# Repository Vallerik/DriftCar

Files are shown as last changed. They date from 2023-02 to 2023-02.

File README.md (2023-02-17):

DriftCar
====
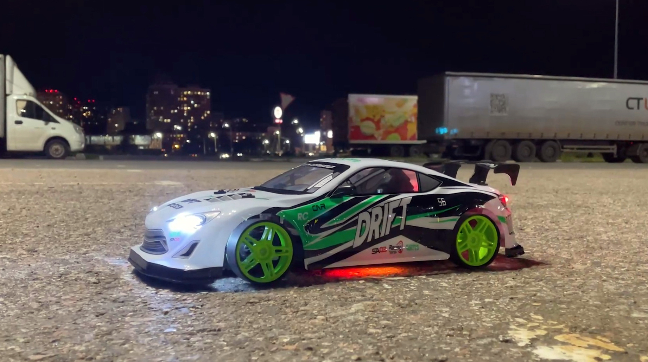
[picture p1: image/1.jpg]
DriftCar

In this project, I showed the completion of a drift car with a complete alteration of electronics and the addition of lighting and music.
What a drift machine is initially capable of:
- The charge of the native battery is enough for 10 minutes, after 7 minutes the car just drives without drifting;
- Discrete control;
- Police lighting;
- Drift around;
- Drift eight.

[Video review of drift cars without modifications.](https://youtu.be/6MPHbPOtivM)

What do I want to do?
- Make front and rear lights;
- Introduce completely your own homemade electronics with proportional steering and gas control;
- Write a program for the typewriter and remote control;
- Put 3S battery;
- Add music to the machine with the ability to switch it from the remote control;
- Make the backlight on the addressable LEDs with the ability to switch it from the remote control;
- Servo steering wheel control.

[Video about drift cars with all the modifications.](https://youtu.be/wygo5vjzIAw)

Required components
====
For electronics, you will need the following components:

For the machine:
- Arduino Nano - 1 piece;
- Servo MG90D - 1 piece;
- HC-12 - 1 piece;
- Board with addressable LEDs - 2 pieces;
- Wires;
- Player DY-SV5W - 1 piece;
- microSD memory card - 1 piece;
- Speaker AIYIMA 5W 4 om - 1 piece;
- Racks for a column - 2 pieces;
- Hardware for the column and brass racks;
- LEDs white 5 mm - 2 pieces;
- LEDs white 3 mm - 4 pieces;
- LEDs red 5mm - 2 pieces;
- Resistors 100 ohm - 6 pcs, 150 ohm - 2 pcs, 200 ohm - 1 pc, 10 kOhm - 1 pc;
- Connectors XH 2.54 3P female - 4 pcs;
- Connectors XH 2.54 3P male - 4 pcs;
- Connector JST SM 2.54 2P female - 1 piece;
- Printed circuit boards.

For remote control:
- Arduino Nano - 1 piece;
- HC-12 - 1 piece;
- Charging board TP4056 with step-up DC-DC converter - 1 piece;
- CJMCU-103 - 2 pieces;
- Two-color LED with a common cathode - 1 pc;
- Resistors 150 ohm - 1 piece, 160 ohm - 1 piece;
- DIP Buttons - 2 pieces;
- Wires;
- Connector JST SM 2.54 2P female - 1 piece;
- Breadboard - 1 piece;
- LiPo 400mA - 1 piece.

For battery:
- Li-ion NCR 18650 with wires - 3 pieces;
- BMS 3S with balancing - 1 piece;
- Connector JST SM 2.54 2P male - 1 piece;
- Wires.

Revision history
====
I started reworking the machine by disassembling and studying its device. I took off all the native electronics with the steering mechanism and began to think about how and where to place all the components.
In this project, I have identified two difficult places for rework:
1. Steering.
I have a rough idea of how the steering should work on a servo, but how to place it and will the small servo have enough power? For me, these were the main questions and fears.
2. Alteration of the remote control.
Since the native equipment of the drift car has discrete control, it will be difficult to convert it to proportional control, according to my feelings, because you need to somehow build variable resistors into the remote control,
and what if it doesn't work? Well, as they say, the eyes are afraid, but the hands do!

It is very important in projects to find difficult places or things that cause the most problems, these things need to be done first and after solving all the difficult tasks, do everything else.
It would be very stupid to abandon the project at an almost finished stage, when all the simplest things have already been done, but you cannot complete the project because of 2 difficult tasks that you decided to postpone.
As a result, you get an abandoned project that needs to be redone or finalized.

After studying the device, I had several options for the location of the components, first of all, I tested the servo and decided on its power.
I thought over the steering mechanism, the location of the servo drive and the device of the control panel. In order to finally decide on the device of the machine and the remote control, then it is necessary to prepare the electronics.
I wrote a program in the Arduino IDE, assembled and debugged the prototype, after that I made a circuit diagram of the electronics of the machine and the remote control.

The device of the new steering mechanism
====
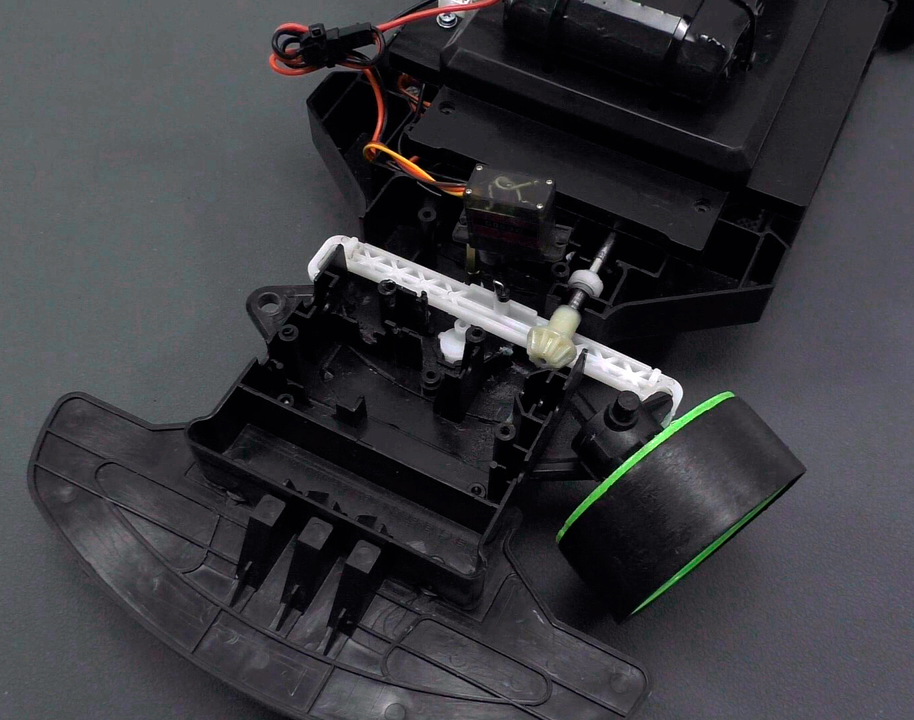
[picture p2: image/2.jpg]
The device of the new steering mechanism

The ideal place to fix the servo coincides with the plastic stand in the case. The second ear of the servo is already screwed to the brass stand in place. 
In the central position of the servo, a rocker with a drilled groove is screwed. A curved pin glued into the steering rack is inserted into this groove. 
The pin is made from the original spring of the steering gear, teeth for the gear were bitten off from the rack itself.
And the only important point, you need to install the rocker in the central position of the servo (90°) and the servo itself is screwed through a spacer printed on a 3D printer. 
The servo drive, turning the rocker, moves the pin along the groove, thereby setting the steering rack in motion. The mechanism works perfectly, 
there is enough servo power, there is no jamming, and I was even surprised how well the arrangement of the components coincided.

Location of electronics
====
In the compartment for the old battery, I screwed the board from the player onto the plastic racks, and fastened the speed controller to the plastic ties.

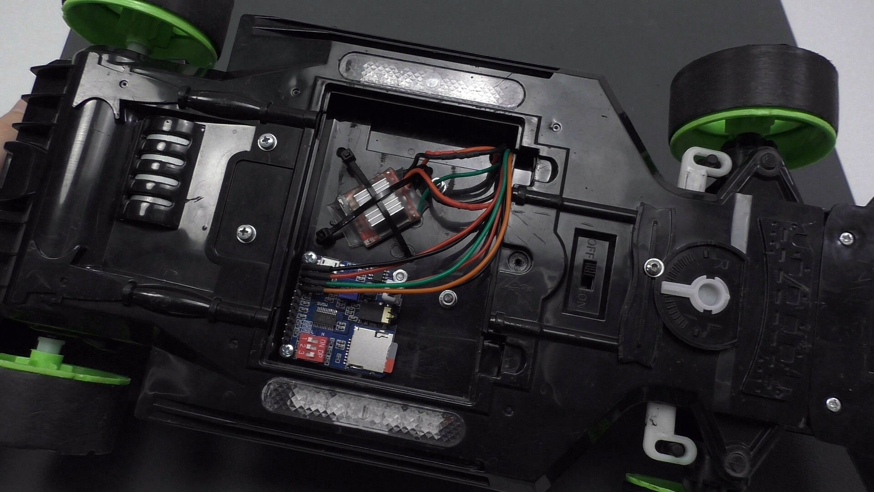
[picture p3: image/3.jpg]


By the way, this regulator needs to be improved to prevent its heating when powered by a 3S battery. The fact is that this speed controller, according to the seller, only supports a 2S battery.
When a 3S battery is connected, the regulator also works, but the diode and transistor start to heat up, I dropped these components, the printed circuit board stopped heating and the regulator works properly.
All components on the PCB support voltages above 12 volts, so everything is fine.

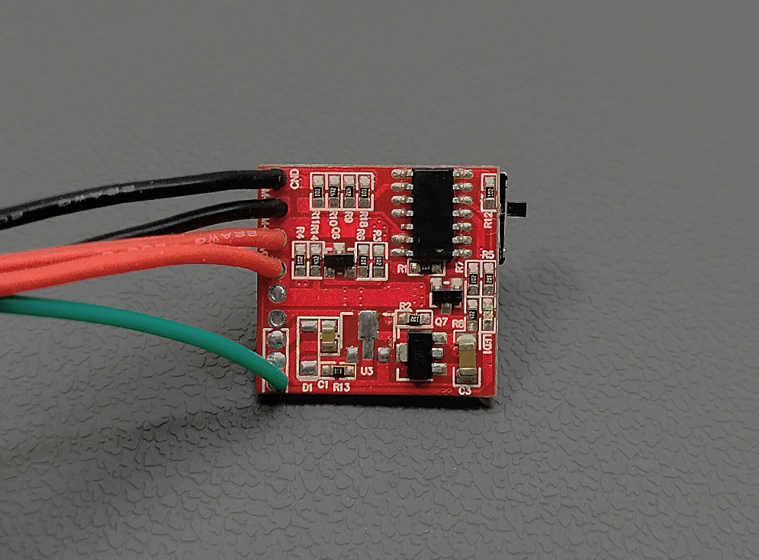
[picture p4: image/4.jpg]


Under the central cover in the middle, there is a board with an Arduino Nano, after which a power board is installed and panels with addressable LEDs are glued on the sides.
The native switch in the front is used to turn off the power, some holes were also made in the case for wires, well, the whole bunch of wires, if possible, was fastened with plastic ties.

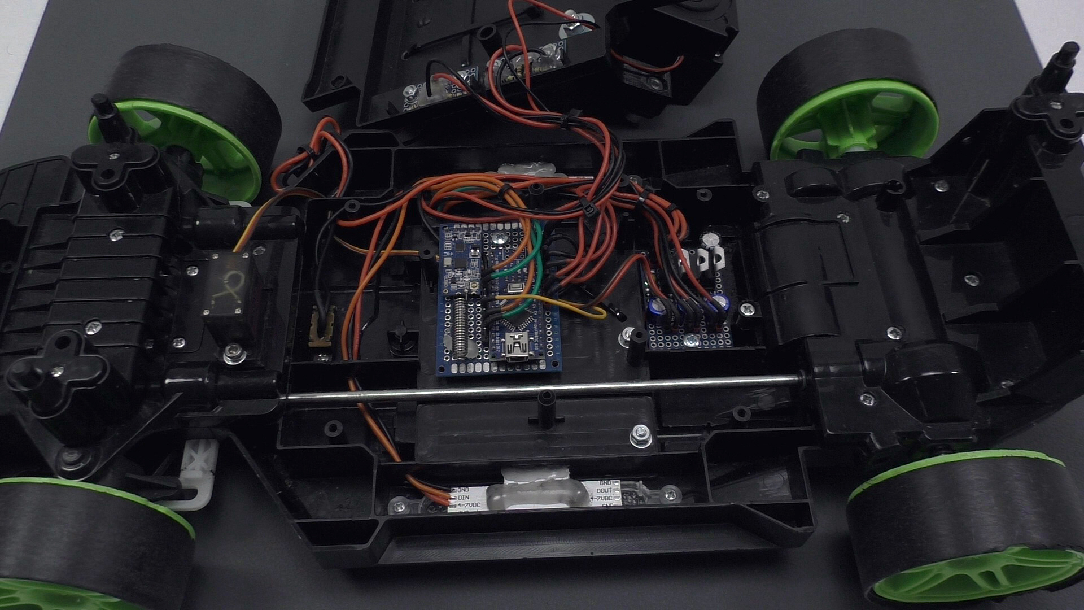
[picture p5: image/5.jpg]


All electronics are connected according to this scheme:
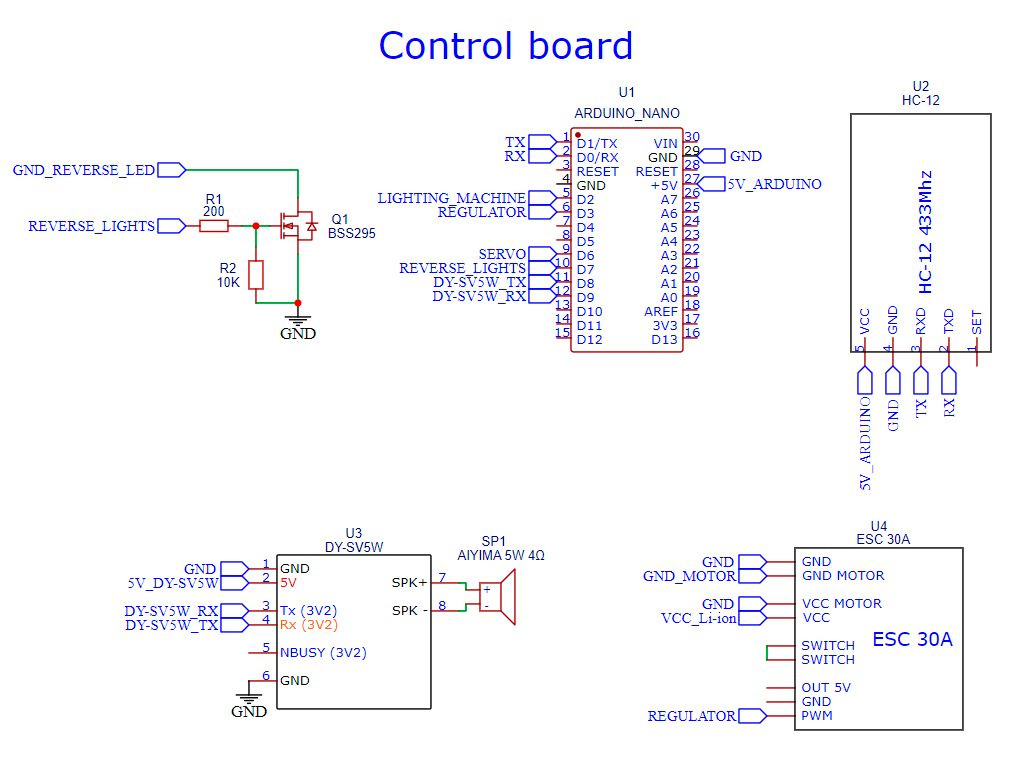
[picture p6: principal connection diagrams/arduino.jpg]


Printed circuit boards
====

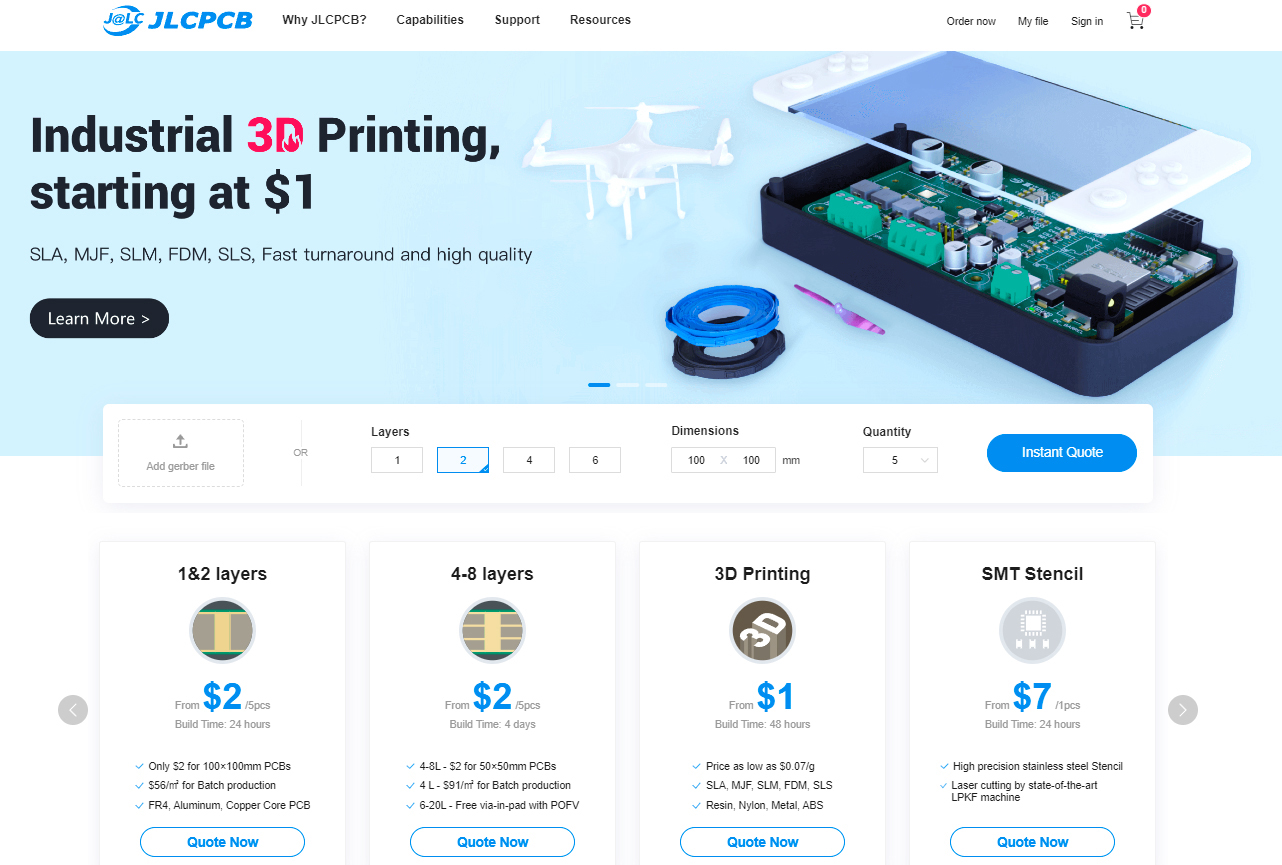
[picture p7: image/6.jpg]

In order not to suffer like me with the manufacture of boards on a breadboard, I recommend ordering the manufacture of printed circuit boards from [JLC PCB](https://jlcpcb.com/RHS). 
This is the largest enterprise for the production of printed circuit boards of industrial quality, of any complexity, of any size.
For just $2 plus shipping, [JLC PCB](https://jlcpcb.com/RHS) will make you five 2-layer 100x100mm PCBs, or five 4-layer 50x50mm PCBs! [JLC PCB](https://jlcpcb.com/RHS) can not only manufacture boards, 
but also assemble them on their surface mount equipment. To place an order, you need to upload an archive with gerber files to the site, in the order itself you can configure the necessary parameters, 
such as the color of the mask, the thickness of the textolite, copper and order the assembly of boards, also [JLC PCB](https://jlcpcb.com/RHS) is engaged in 3D printing, 
making stencils for SMT mounting and all this makes in the shortest possible time and with the best quality, so I recommend them.
I made all the listed printed circuit boards from breadboards, soldering the tracks with solder. 
This method of manufacturing printed circuit boards is not always suitable and it is quite difficult to think through the passage of all the tracks, 
and the soldering process itself is complicated if you want to do it neatly and beautifully. Therefore, I recommend ordering printed circuit boards in production, do not suffer, 
do not repeat my mistakes :)

[https://jlcpcb.com/](https://jlcpcb.com/RHS)

GitHub link to download PCB gerber file: 
https://github.com/Vallerik/DriftCar/tree/main/gerber

Battery assembly
====
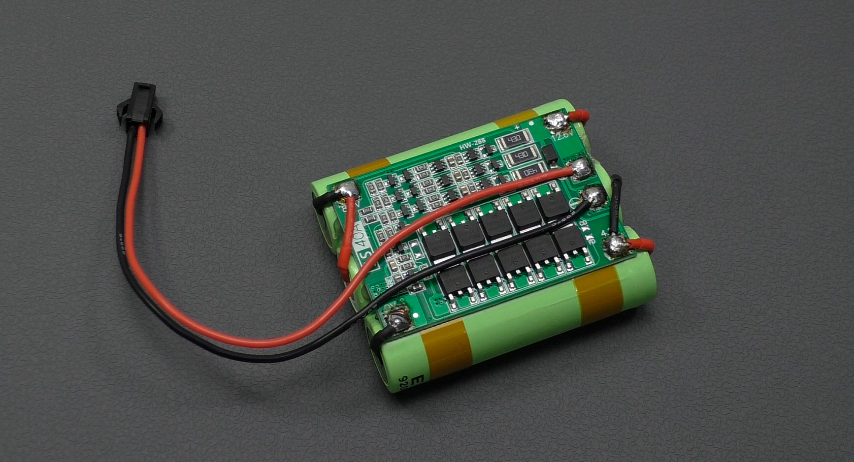
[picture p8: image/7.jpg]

There is nothing complicated in assembling the battery, I think everything is clear just from the photo.
The wires of each can of 18650 are soldered to the corresponding BMS pin of the board, as in this photo.
To connect the battery, a wire with a JST SM 2.54 2P male connector is soldered to the BMS.

Headlights
====
Holes are drilled on the body in the center of all the painted headlights and LEDs are glued with hot glue. 
### Beforehand, it is necessary to solder the wires to the LEDs according to the scheme:
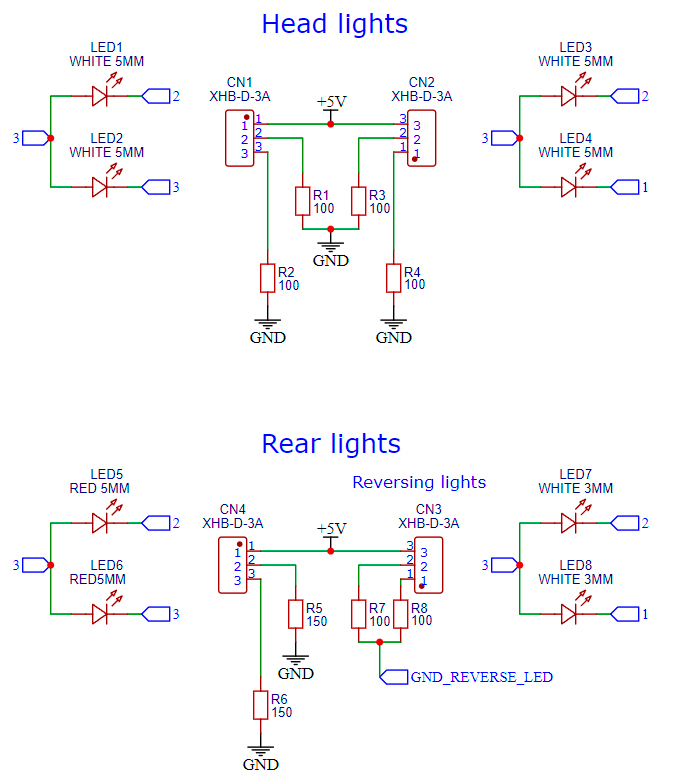
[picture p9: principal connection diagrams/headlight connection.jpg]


The headlights are made from 3 and 5mm white LEDs. Reversing lights made of white 3mm LEDs. The oversized red headlights are made from matte red 5mm LEDs.
The wires from the headlights will be connected to the XH 2.54 3P connectors (Each wire is connected according to its color mark), 
printed circuit boards with these connectors are screwed to the side of the central cover of the machine.

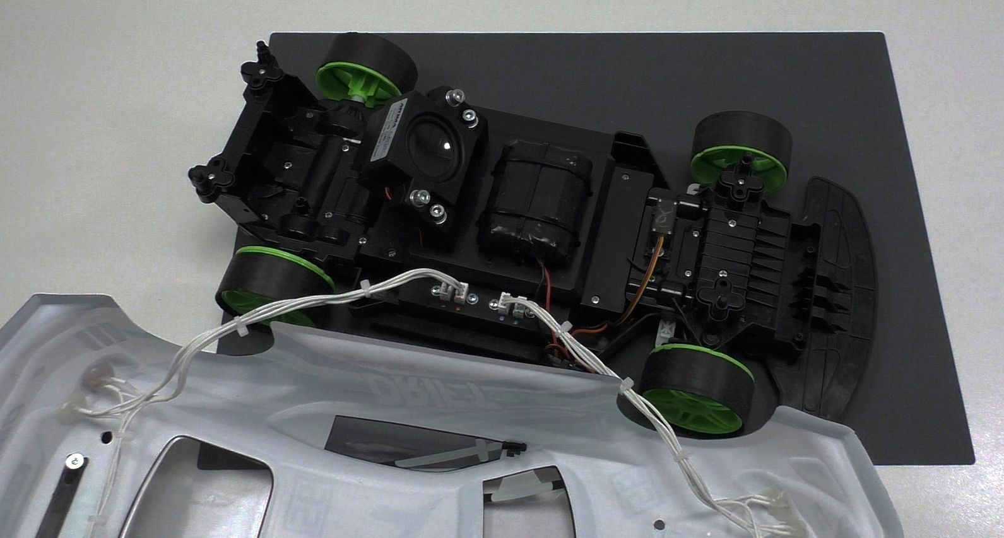
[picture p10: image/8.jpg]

Racks with a speaker are screwed to the same cover and the battery is attached to plastic ties.

Remote control modification
====
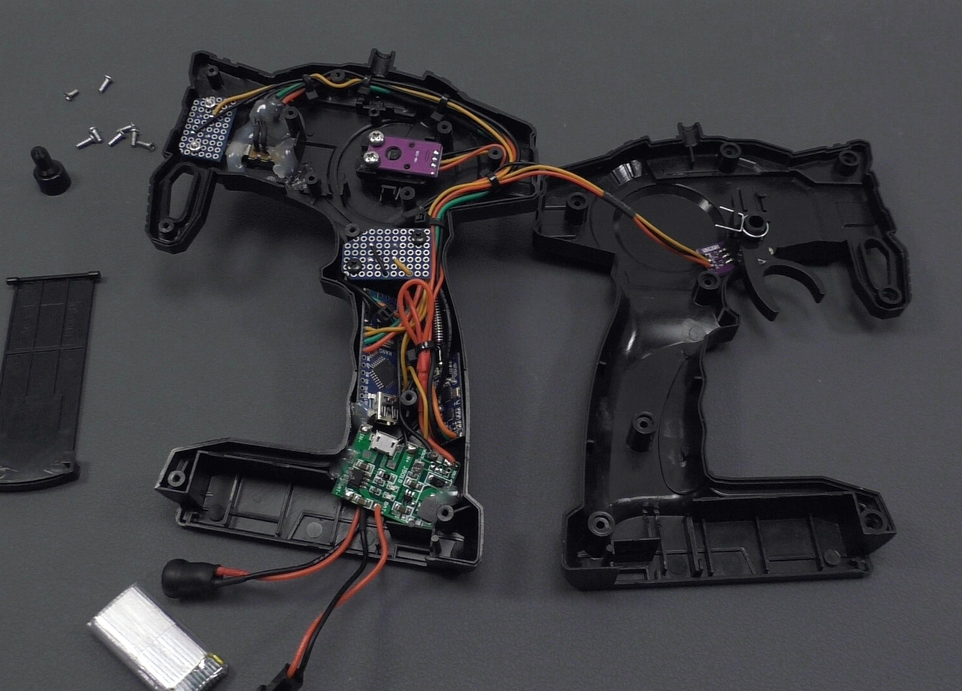
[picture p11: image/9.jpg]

To remake the control panel, the first thing I thought about was how to install the CJMCU-103 modules. To do this, I printed on a 3D printer a special mount and pins for turning the CJMCU-103, 
these pins are glued into the trigger and steering shaft. The first CJMCU-103 steering wheel module is screwed to the mount, and the second CJMCU-103 module is screwed to the control box cover.
Also, for the remote control, two printed circuit boards were cut out for the buttons, a two-color LED was glued in, a switch and a resistor for setting the charging current was changed on the green charging module, 
for a li-po battery with a capacity of 400 mA, I set the charging current to 300 mA. Charging takes place with a USB cable that plugs into a 5.5x2.1 mm jack.
There is nothing else special in the remote control, and well, I also changed my native antenna to a small one printed on a 3D printer. In general, the remote turned out great!
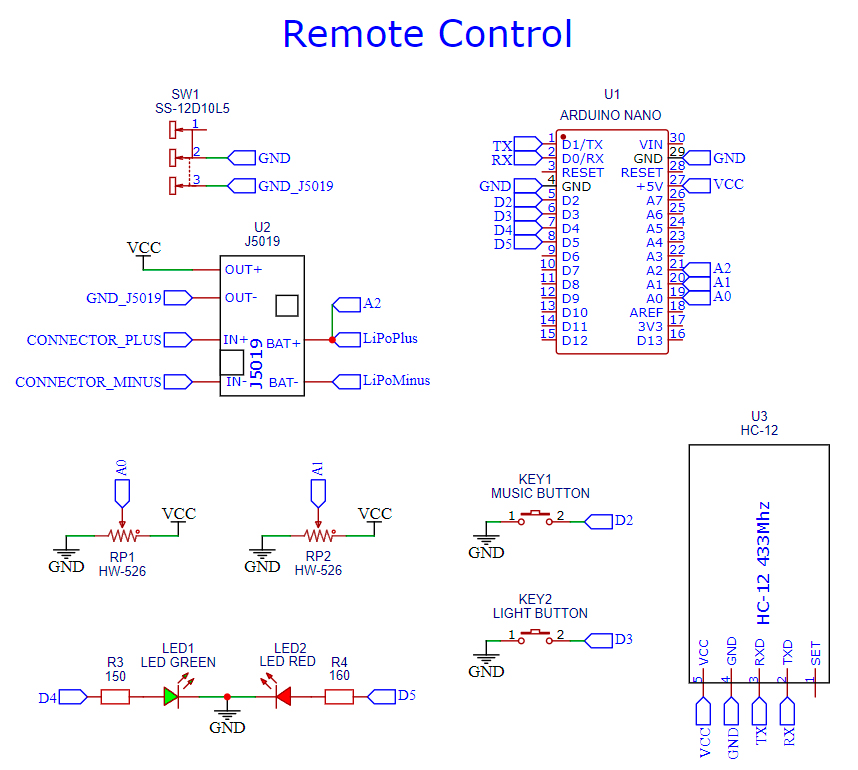
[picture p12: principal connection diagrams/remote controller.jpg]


Project results
====
Now let me summarize, has the car started to drift better? The result, of course, was not the same as I expected, but the car became more cheerful to drive from a 3S battery, due to the proportional control, 
the car became better controlled and, of course, it is better to look with headlights and RGB backlight. A loud speaker makes the bass vibrate and play the whole body, 
these are indescribable sensations of the joy of a working project. My main goal is accomplished, to make a musical drift car with my homemade electronics. From the remote control, 
I can turn on, switch music and backlight, the backlight still has 7 modes of operation, well, in general, I'm exhausted, but satisfied. I will not say that I am an expert in this matter, 
I just set a goal for myself and achieved it. And in this project, I shared my experience and, as a result, I want to warn you that developing your own electronics and modifying such toys is not as easy as it seems. 
If you want to repeat the project after me or do something similar, I would advise you to install ready-made electronics, a receiver, a speed controller, a purchased battery with equipment, 
it will come out easier, cheaper and faster.

Links to other important sources
------------
* [Thingiverse](https://www.thingiverse.com/yourobotics/designs) 3D Model for time-lapse photography.
* [VK group](https://vk.com/yourobotics) My group on the social network "Vkontakte".
* [YouRobotics](https://www.youtube.com/channel/UCt6Rz9BVB6opYcUrAq6mwWA) My YouTube channel.
------------
Made by: Valery Zalit

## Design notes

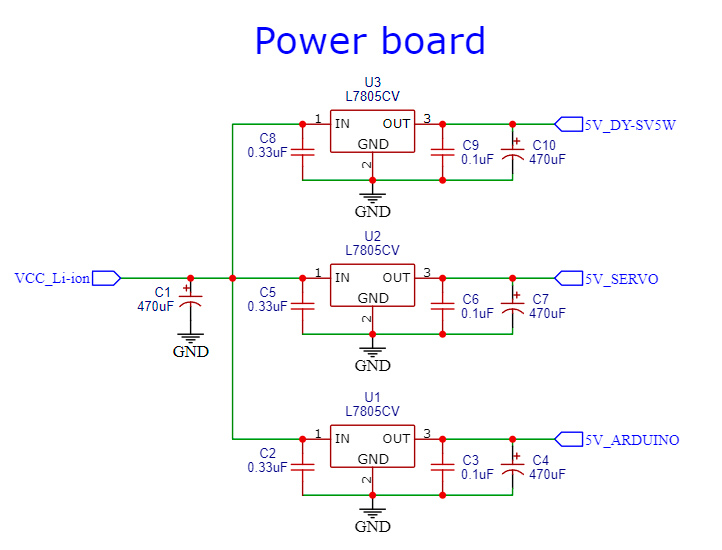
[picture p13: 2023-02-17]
principal connection diagrams/power board.jpg

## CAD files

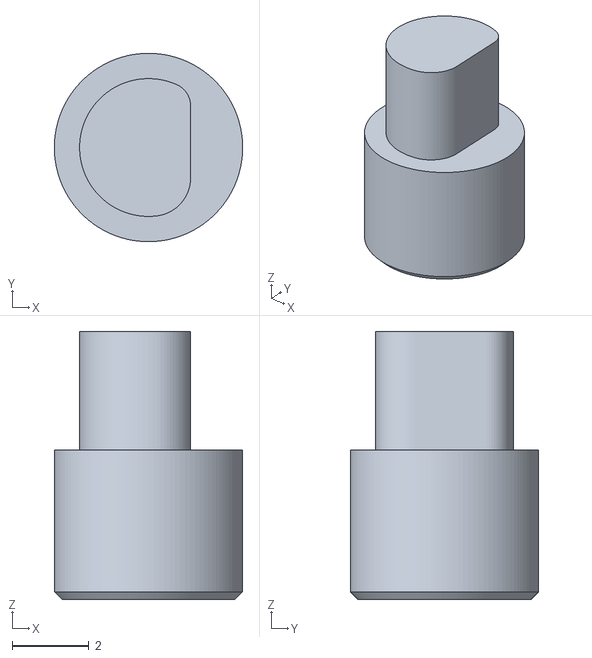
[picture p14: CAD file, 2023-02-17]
3d models/Rudder pin.stl
4.92 x 4.92 x 7.00

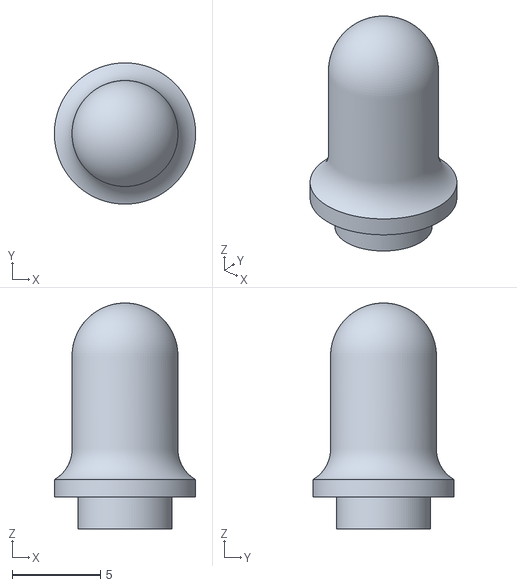
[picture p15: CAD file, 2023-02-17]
3d models/Remote control antenna.stl
8.00 x 8.00 x 12.8

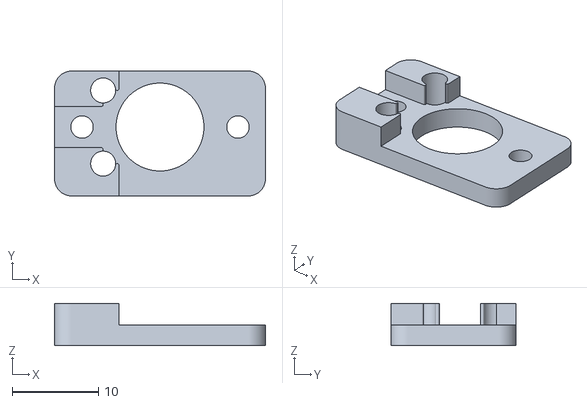
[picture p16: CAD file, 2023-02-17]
3d models/Plate for CJMCU-103.stl
24.5 x 14.5 x 4.90

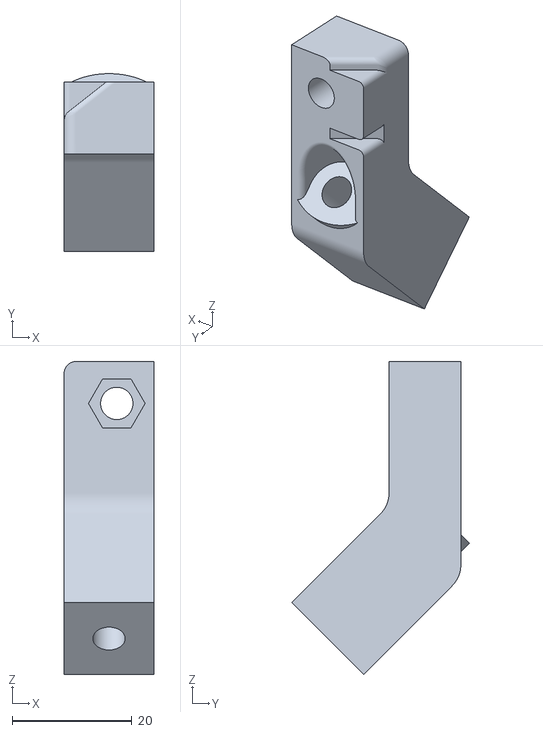
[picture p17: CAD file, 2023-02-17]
3d models/Speaker stand.stl
15.0 x 29.7 x 52.3

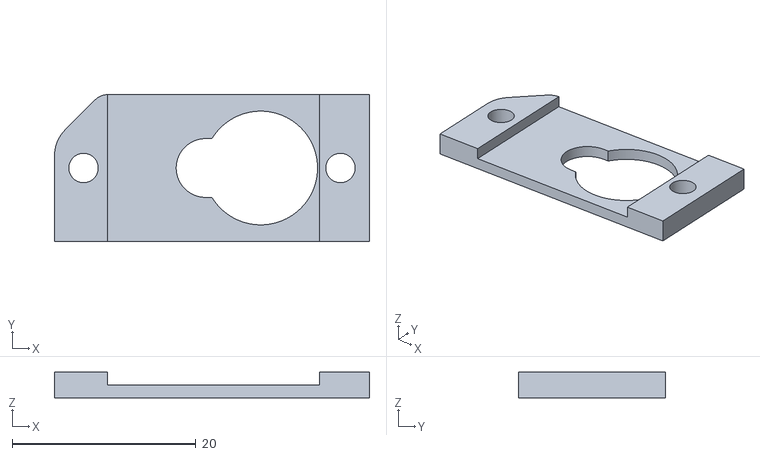
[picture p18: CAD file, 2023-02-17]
3d models/Servo spacer.stl
34.3 x 16.0 x 2.80

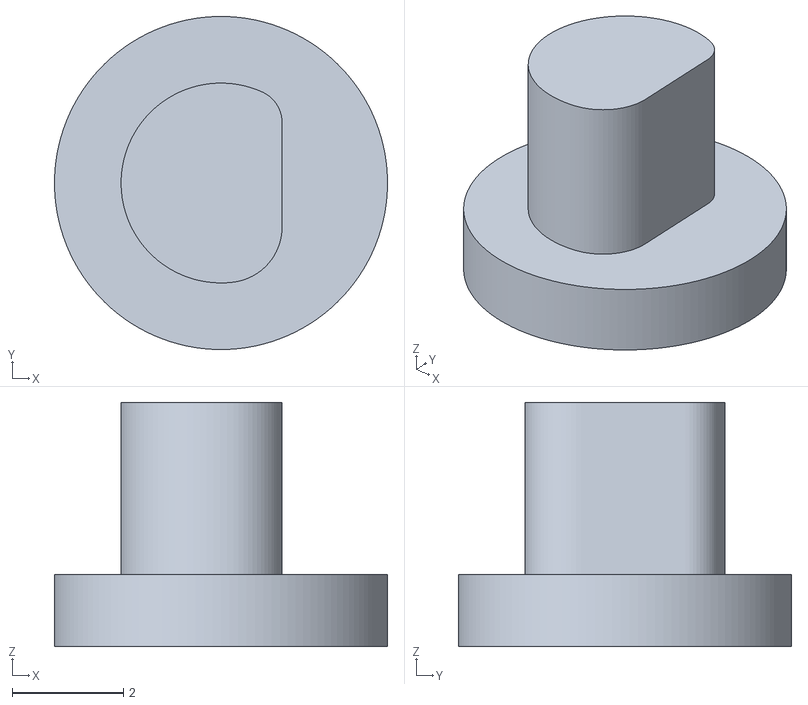
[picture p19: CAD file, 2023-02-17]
3d models/Throttle pin.stl
6.00 x 6.00 x 4.40

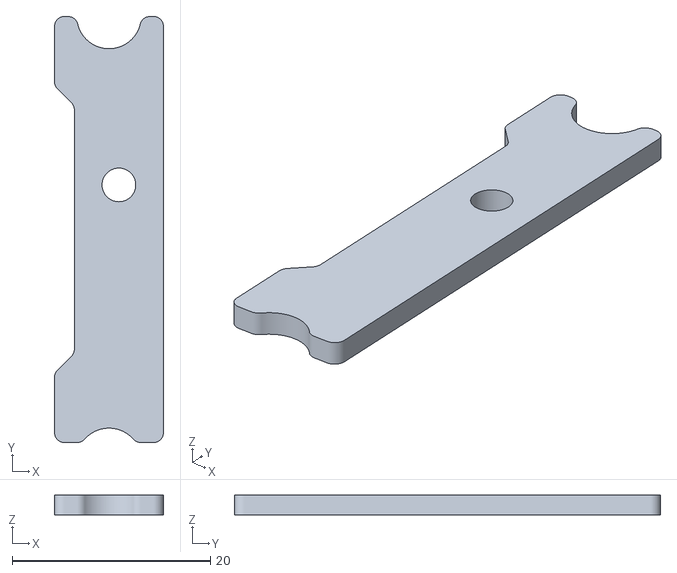
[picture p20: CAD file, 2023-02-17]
3d models/Spacer for servo stand.stl
11.0 x 43.0 x 2.00

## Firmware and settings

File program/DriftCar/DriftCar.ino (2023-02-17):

//Settings
#define MUSIC_OFF_ON_COMMAND 1
#define MUSIC_NEXT_COMMAND 2
#define ON_OFF_BACKLIGHT 3
#define NEXT_ILLUMINATION 4
#define NUMBER_OF_BACKLIGHT_MODES 7 //Number of backlight modes
#define CORNER_CORRECTION -11 //(-право)
#define CENTER_ANGLE 90 CORNER_CORRECTION //Center wheel position
#define MAX_ANGLE 124 //Maximum steering angle
#define MIN_ANGLE 44 //Minimum steering angle

//Libraries
#include <avr/wdt.h>
#include <Arduino.h>
#include "DYPlayerArduino.h"
#include <SoftwareSerial.h>
#include <Servo.h>

#include <LiquidCrystal_I2C.h>

SoftwareSerial mySerial(9, 8); // RX, TX
DY::Player player(&mySerial);
Servo servo;
Servo motor;

#define LEDPIN 2
#define NUMLEDS 8     //Number of LEDs
#include <microLED.h>
#include <FastLEDsupport.h>
microLED<NUMLEDS, LEDPIN, MLED_NO_CLOCK, LED_WS2818, ORDER_GRB, CLI_AVER> strip;

extern CRGBPalette16 myRedWhiteBluePalette;
extern const TProgmemPalette16 myRedWhiteBluePalette_p PROGMEM;

//Pins
#define M_REGULATOR 3
#define RUDDER_SERVO 6
#define REVERSE_LEDS 7


boolean playerStatus = 0;
boolean triggerFlag = 0;
boolean musicStatus = 0;
boolean backlightStatus = 0;
boolean noData = 0;
boolean emergencyStop = 0;

int backlightMode = 0;

unsigned long ledTimer = 0;
unsigned long noDataTimer = 0;

struct Str {
  uint8_t direction;
  int16_t speed;
  uint8_t angle;
  uint8_t command;
};

Str buf;

void setup() {
  Serial.begin(9600);
  mySerial.begin(9600);
  servo.attach(RUDDER_SERVO);
  motor.attach(M_REGULATOR);

  pinMode(REVERSE_LEDS, OUTPUT);

  player.begin();
  player.setVolume(95); //Set the volume to 95%
  player.setCycleMode(DY::PlayMode::Random);
  player.stop();

  strip.setBrightness(64);
  buf.angle = CENTER_ANGLE;

  wdt_enable(WDTO_1S);
}

void ReceiveData() {
  Serial.readBytes((byte*)&buf, sizeof(buf));
}

void PlayerControl(int command) {
  servo.detach();
  motor.detach();

  if (command == 0) {
    musicStatus = 0;  //Turn off the music
    player.stop();
  }

  if (command == 1) {
    musicStatus = 1;  //Turn on the music
    player.play();
  }

  if (command == 2 && musicStatus == 1) {
    player.next();  //Next music
  }

  motor.attach(M_REGULATOR);
  servo.attach(RUDDER_SERVO);
}

void loop() {
  ControlCar();

  if (Serial.available() > 0) {
    ReceiveData();
    noData = 0;
    emergencyStop = 0;
  } else {
    if (noData == 0) {
      noDataTimer = millis();
      noData = 1;
    }
    if (noData == 1 && emergencyStop == 0 && (millis() - noDataTimer) > 500) {
      buf.direction = 0;
      buf.speed = 1500;
      player.stop();
      offLeds(); //Turn off backlight
      backlightMode = 0;
      emergencyStop = 1;
    }
  }

  carBacklight();
  wdt_reset();
}

void ControlCar() {
  if (buf.direction == 0) {
    motor.writeMicroseconds(1500);
    digitalWrite(REVERSE_LEDS, LOW);
  }

  if (buf.direction == 1) {
    motor.writeMicroseconds(buf.speed);
    digitalWrite(REVERSE_LEDS, LOW);
  }

  if (buf.direction == 2) {
    motor.writeMicroseconds(buf.speed);
    digitalWrite(REVERSE_LEDS, HIGH);
  }

  if (buf.angle >= MAX_ANGLE) {
    buf.angle = MAX_ANGLE;
  }

  if (buf.angle <= MIN_ANGLE) {
    buf.angle = MIN_ANGLE;
  }

  servo.write(buf.angle); //Turning the servo

  if (buf.command == MUSIC_OFF_ON_COMMAND && triggerFlag == 0) { //Turning music on and off
    triggerFlag = 1;
    playerStatus = 1 - playerStatus;
    PlayerControl(playerStatus);
  }

  if (buf.command == MUSIC_NEXT_COMMAND && triggerFlag == 0) { //Switching music
    triggerFlag = 1;
    PlayerControl(2);
  }

  if (buf.command == 3 && triggerFlag == 0) { //Turning the backlight on and off
    triggerFlag = 1;
    backlightStatus = backlightStatus - 1;
    backlightMode = 1;

    ledTimer = millis();

    if (backlightStatus == 0) {
      offLeds(); //Turn off the backlight
      backlightMode = 0;
    }
  }

  if (buf.command == NEXT_ILLUMINATION && triggerFlag == 0 && backlightStatus == 1) { //Switching backlight mode
    triggerFlag = 1;
    backlightMode++;
    if (backlightMode > NUMBER_OF_BACKLIGHT_MODES) {
      backlightMode = 1;
    }

  }

  if (buf.command == 0 && triggerFlag == 1) {
    triggerFlag = 0;
  }

}

void offLeds() {
  strip.leds[0] = mBlack;
  strip.leds[1] = mBlack;
  strip.leds[2] = mBlack;
  strip.leds[3] = mBlack;
  strip.leds[4] = mBlack;
  strip.leds[5] = mBlack;
  strip.leds[6] = mBlack;
  strip.leds[7] = mBlack;
  strip.show();
}

void carBacklight() {
  if ( ((millis() - ledTimer) > 40) && backlightStatus == 1 ) {
    motor.detach();
    static byte count = 0;
    static int count2 = 0;
    count = count + 4;
    count2 += 10;
    strip.begin();
    for (int i = 0; i < NUMLEDS; i++) {
      switch (backlightMode) {
        case 1: //Green
          strip.leds[0] = mGreen;
          strip.leds[1] = mGreen;
          strip.leds[2] = mGreen;
          strip.leds[3] = mGreen;
          strip.leds[4] = mGreen;
          strip.leds[5] = mGreen;
          strip.leds[6] = mGreen;
          strip.leds[7] = mGreen;
          strip.show();
          break;

        case 2: //Blue
          strip.leds[0] = mBlue;
          strip.leds[1] = mBlue;
          strip.leds[2] = mBlue;
          strip.leds[3] = mBlue;
          strip.leds[4] = mBlue;
          strip.leds[5] = mBlue;
          strip.leds[6] = mBlue;
          strip.leds[7] = mBlue;
          strip.show();
          break;

        case 3: //Red
          strip.leds[0] = mRed;
          strip.leds[1] = mRed;
          strip.leds[2] = mRed;
          strip.leds[3] = mRed;
          strip.leds[4] = mRed;
          strip.leds[5] = mRed;
          strip.leds[6] = mRed;
          strip.leds[7] = mRed;
          strip.show();
          break;

        case 4:
          strip.send(CRGBtoData(ColorFromPalette(RainbowColors_p, count + i * 3, 255, LINEARBLEND)));
          break;

        case 5:
          strip.send(CRGBtoData(ColorFromPalette(RainbowStripeColors_p, count + i * 3, 255, NOBLEND)));
          break;

        case 6:
          strip.send(CRGBtoData(ColorFromPalette(RainbowColors_p, count + i * 3, 255, LINEARBLEND)));
          break;

        case 7:
          strip.send(CRGBtoData(ColorFromPalette(myRedWhiteBluePalette_p, count + i * 3, 255, NOBLEND)));
          break;

      }
    }
    strip.end();
    motor.attach(M_REGULATOR);
    ledTimer = millis();
  }
}


const TProgmemPalette16 myRedWhiteBluePalette_p PROGMEM =
{
  CRGB::Red,
  CRGB::Gray,
  CRGB::Blue,
  CRGB::Black,

  CRGB::Red,
  CRGB::Gray,
  CRGB::Blue,
  CRGB::Black,

  CRGB::Red,
  CRGB::Red,
  CRGB::Gray,
  CRGB::Gray,
  CRGB::Blue,
  CRGB::Blue,
  CRGB::Black,
  CRGB::Black
};

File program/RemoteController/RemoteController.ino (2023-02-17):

/*
   Remote control program for drift cars
*/

#include <avr/wdt.h>

//Settings
#define MUSIC_OFF_ON_COMMAND 1
#define MUSIC_NEXT_COMMAND 2
#define ON_OFF_BACKLIGHT 3
#define NEXT_ILLUMINATION 4

//Steering wheel
#define CORNER_CORRECTION -11 //Correction of the central position of the wheels (- right, + left)
#define MIN_ANGLE 44 //Minimum steering angle
#define CENTER_ANGLE 90 CORNER_CORRECTION // Servo wheel center position + correction
#define MAX_ANGLE 124 //Max steering angle

#define WHEEL_MINIMUM_RESISTOR_VALUE 377 //Minimum variable resistor value
#define WHEEL_AVERAGE_RESISTOR_VALUE 509 //Average value of the variable resistor
#define WHEEL_MAXIMUM_RESISTOR_VALUE 623 //Maximum value of the variable resistor
#define WHEEL_DEADBAND 5 //Deadband


//Throttle lever
#define SPEED_AVERAGE_RESISTOR_VALUE 543 //Middle speed position
#define SPEED_MAXIMUM_RESISTOR_VALUE 632 // Maximum throttle position
#define SPEED_MINIMUM_RESISTOR_VALUE 470 //Minimum throttle position
#define SPEED_DEADBAND 5 //Deadband

//Battery overdischarge protection settings
#define OVER_DISCHARGE_VOLTAGE 3.1 //Battery over-discharge protection voltage
#define BOARD_SUPPLY_VOLTAGE 5.0 //Board supply voltage (needed to read the voltage)

//Pins
#define VARIABLE_RESISTOR_WHEEL A1
#define VARIABLE_RESISTOR_SPEED A0
#define VOLTMETER A2
#define MUSIC_BUTTON 2
#define LIGHT_BUTTON 3
#define LED_GREEN 4
#define LED_RED 5

int carSpeed;
int rotationAngle;
int rotationAngle2;

float volt = 0;

boolean overdischargeProtection = false;
boolean mb_flag = 0;
boolean mb_hold_flag = 0;
boolean lb_flag = 0;
boolean lb_hold_flag = 0;

unsigned long mb_last_press = 0;
unsigned long lb_last_press = 0;
unsigned long startTime = 0;

struct Str {
  uint8_t direction;
  int16_t speed;
  uint8_t angle;
  uint8_t command;
};
Str buf;


void setup() {
  Serial.begin(9600);

  pinMode(VARIABLE_RESISTOR_WHEEL, INPUT);
  pinMode(VARIABLE_RESISTOR_SPEED, INPUT);
  pinMode(VOLTMETER, INPUT);
  pinMode(MUSIC_BUTTON, INPUT_PULLUP);
  pinMode(LIGHT_BUTTON, INPUT_PULLUP);
  pinMode(LED_GREEN, OUTPUT);
  pinMode(LED_RED, OUTPUT);

  startTime = millis();

  digitalWrite(LED_GREEN, HIGH);
  wdt_enable(WDTO_1S);
}

void sendingData() {
  Serial.write((byte*)&buf, sizeof(buf)); //Sending data
  if (buf.command != 0) {
    buf.command = 0;
  }
  startTime = millis();
}


void resistorProcessing() {
  carSpeed = analogRead(VARIABLE_RESISTOR_WHEEL);
  rotationAngle = analogRead(VARIABLE_RESISTOR_SPEED);

  if (carSpeed > SPEED_MAXIMUM_RESISTOR_VALUE) {
    carSpeed = SPEED_MAXIMUM_RESISTOR_VALUE;
  }

  if (carSpeed < SPEED_MINIMUM_RESISTOR_VALUE) {
    carSpeed = SPEED_MINIMUM_RESISTOR_VALUE;
  }

  if ((rotationAngle < WHEEL_AVERAGE_RESISTOR_VALUE + WHEEL_DEADBAND) || (rotationAngle > WHEEL_AVERAGE_RESISTOR_VALUE - WHEEL_DEADBAND)) {
    buf.angle = CENTER_ANGLE;
  }

  if (rotationAngle > WHEEL_AVERAGE_RESISTOR_VALUE + WHEEL_DEADBAND) {
    buf.angle = map(rotationAngle, WHEEL_AVERAGE_RESISTOR_VALUE + WHEEL_DEADBAND, WHEEL_MAXIMUM_RESISTOR_VALUE, CENTER_ANGLE, MIN_ANGLE);
  }

  if (rotationAngle < WHEEL_AVERAGE_RESISTOR_VALUE - WHEEL_DEADBAND) {
    buf.angle = map(rotationAngle, WHEEL_AVERAGE_RESISTOR_VALUE - WHEEL_DEADBAND, WHEEL_MINIMUM_RESISTOR_VALUE, CENTER_ANGLE, MAX_ANGLE);
  }

  if ((carSpeed < SPEED_AVERAGE_RESISTOR_VALUE + SPEED_DEADBAND) || (carSpeed > SPEED_AVERAGE_RESISTOR_VALUE - SPEED_DEADBAND)) {
    buf.speed = 1500;
    buf.direction = 0;
  }

  if (carSpeed > SPEED_AVERAGE_RESISTOR_VALUE + SPEED_DEADBAND) {
    buf.speed = map(carSpeed, SPEED_AVERAGE_RESISTOR_VALUE + SPEED_DEADBAND, SPEED_MAXIMUM_RESISTOR_VALUE, 1500, 700);
    buf.direction = 1;
  }

  if (carSpeed < SPEED_AVERAGE_RESISTOR_VALUE - SPEED_DEADBAND) {
    buf.speed = map(carSpeed, SPEED_AVERAGE_RESISTOR_VALUE - SPEED_DEADBAND, SPEED_MINIMUM_RESISTOR_VALUE, 1500, 2200);
    buf.direction = 2;
  }
}


void buttons() {
  //Backlight change button
  if (digitalRead(LIGHT_BUTTON) == 0 && lb_flag == 0) {
    lb_flag = 1;
    lb_last_press = millis();
  }

  if (digitalRead(LIGHT_BUTTON) == 0 && lb_hold_flag == 0 && (millis() - lb_last_press) > 1000) {
    lb_hold_flag = 1;
    buf.command = ON_OFF_BACKLIGHT;

  }

  if (digitalRead(LIGHT_BUTTON) == 1 && lb_flag == 1) {
    if (lb_hold_flag == 0 && (millis() - lb_last_press) > 100) {
      buf.command = NEXT_ILLUMINATION;
    }

    lb_flag = 0;
    lb_hold_flag = 0;
  }


  //Button to change and turn on music
  if (digitalRead(MUSIC_BUTTON) == 0 && mb_flag == 0) {
    mb_flag = 1;
    mb_last_press = millis();
  }

  if (digitalRead(MUSIC_BUTTON) == 0 && mb_hold_flag == 0 && (millis() - mb_last_press) > 1000) {
    mb_hold_flag = 1;
    buf.command = MUSIC_OFF_ON_COMMAND;
  }

  if (digitalRead(MUSIC_BUTTON) == 1 && mb_flag == 1) {
    if (mb_hold_flag == 0 && (millis() - mb_last_press) > 80) {
      //Код нажатия
      buf.command = MUSIC_NEXT_COMMAND;
    }

    mb_flag = 0;
    mb_hold_flag = 0;
  }
}

void loop() {
  volt = analogRead(VOLTMETER);
  if (((volt * BOARD_SUPPLY_VOLTAGE) / 1024) <= OVER_DISCHARGE_VOLTAGE) {
    overdischargeProtection = true;
    digitalWrite(LED_GREEN, LOW);
    digitalWrite(LED_RED, HIGH);
  }

  if (overdischargeProtection == false) {
    resistorProcessing();
    buttons();

    if ((millis() - startTime) > 50) {
      sendingData();
    }
  }
  wdt_reset();
}
